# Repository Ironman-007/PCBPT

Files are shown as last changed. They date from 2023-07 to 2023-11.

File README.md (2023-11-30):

# PCBPT (PCB Probe tester)
## The PCBPT_V3 is the latest working version (the one I showed at UIST'23).

This is a system that can help directly connect the schematic of the PCB design with test equipment (oscilloscope. etc,). When doing PCB debugging, we would need to use our hands to hold the oscilloscope probes, and our hands can not be that precise and table. Sometimes our hands are not enough, and we need to go from schematic and PCB layout back and forth to find a proper pad for the signal and place a probe on it.

The PCBPT connects the Sch with the oscilloscope. The user can choose a signal they want to check on the Sch, and the system will choose a proper pad and place a probe on the pad. Then the user can just check the output from the oscilloscope. All the user needs to do is select signals from Sch and check the output.

## PCBPT_V1.0

The first version of PCBPT is here:
https://www.media.mit.edu/projects/pcb-probe-tester/overview/

It's very rough. The machine design is not that perfect. The motor I used is [28BYJ-48](https://www.amazon.com/ELEGOO-28BYJ-48-ULN2003-Stepper-Arduino/dp/B01CP18J4A). It's very slow. The software is not that good, either. I have a separate GUI for the signal choosing. However, what I want is to choose the signal from the EDA, or make a GUI with the Sch and choose the signal from the SCH.

## PCBPT_V2.0
### Mechanical
The new machine design (I really love the Prusa color!).

<p align="center">
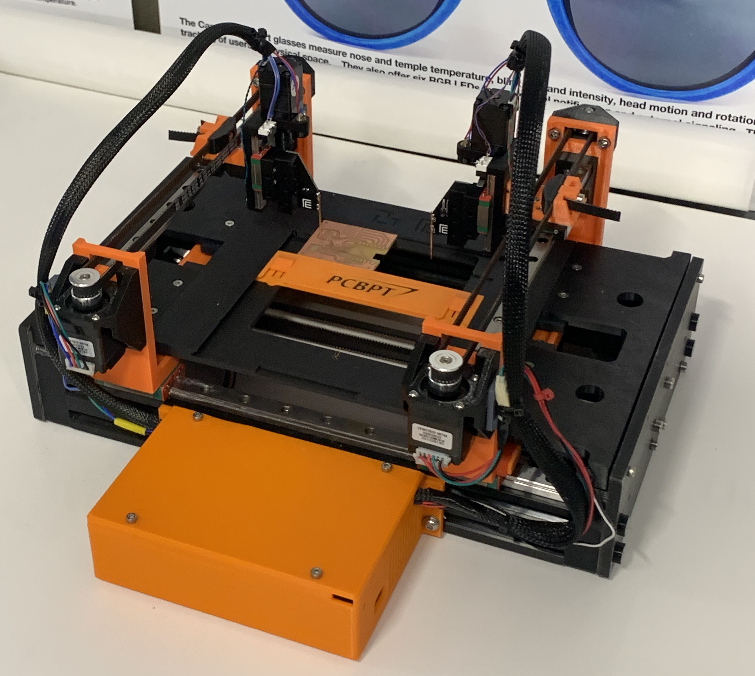
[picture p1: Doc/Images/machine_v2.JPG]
  
</p>

### Electronics
The first version of the main control board is a modular design. Each module can control a stepper motor and a servo. Each module is an RP2040 XIAO + A4988 stepper driver. The host is an ESP32 module.

<p align="center">
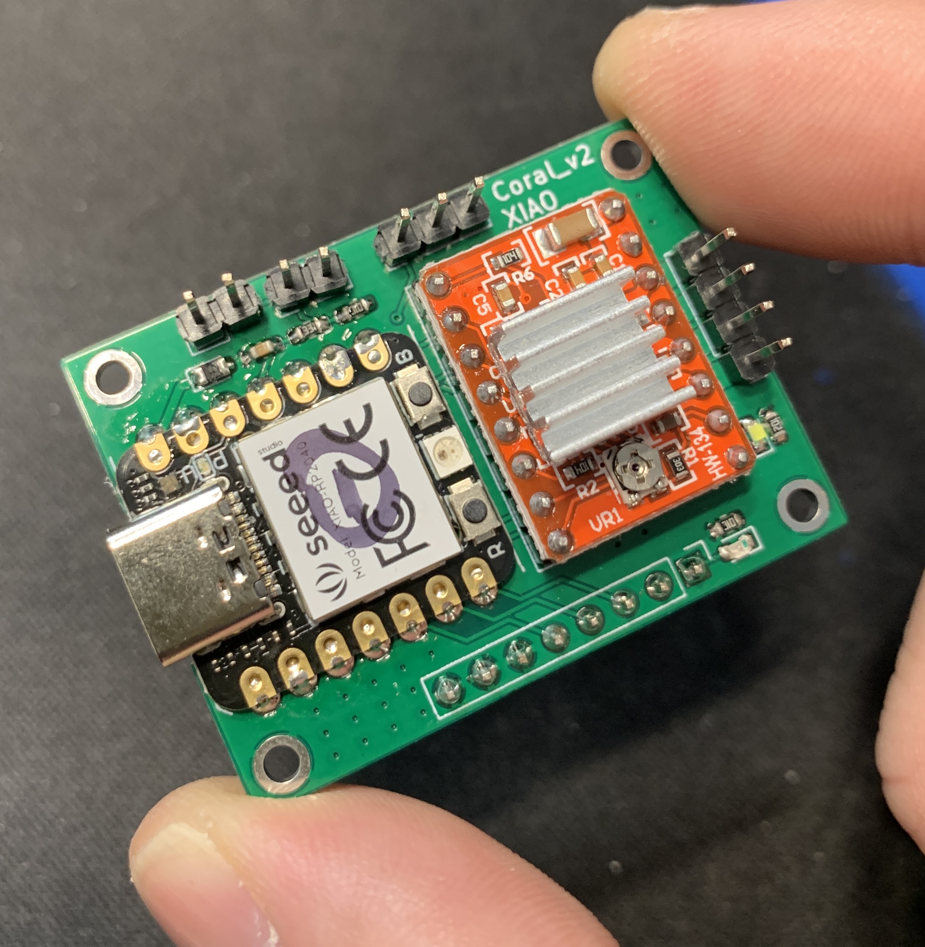
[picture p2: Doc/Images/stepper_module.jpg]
  
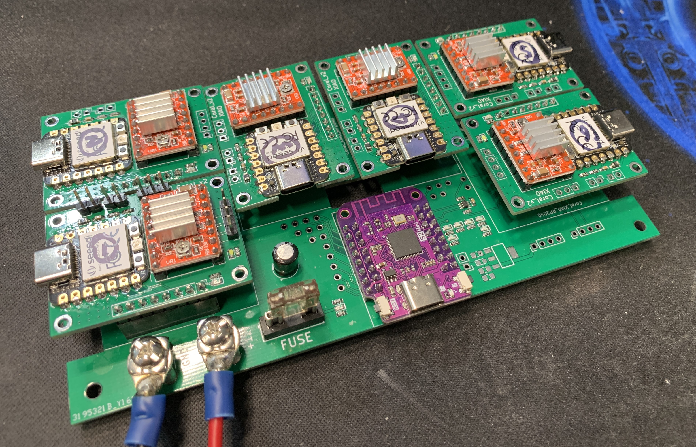
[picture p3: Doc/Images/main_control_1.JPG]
  
</p>

All stepper control modules are connected with the ESP32 module with I2C. The Host runs CircuitPython and is responsible for handling commands from the GUI and sending commands to each stepper control module.
This design is unnecessarily complicated compared with the function of the machine.

The second version of the main control board is a single board. One RPi Pico W module + 6 A4988 driver modules.
The probes are in vertical motion, and each probe is a triangle PCB board with a pogo pin soldered on the edge.

<p align="center">
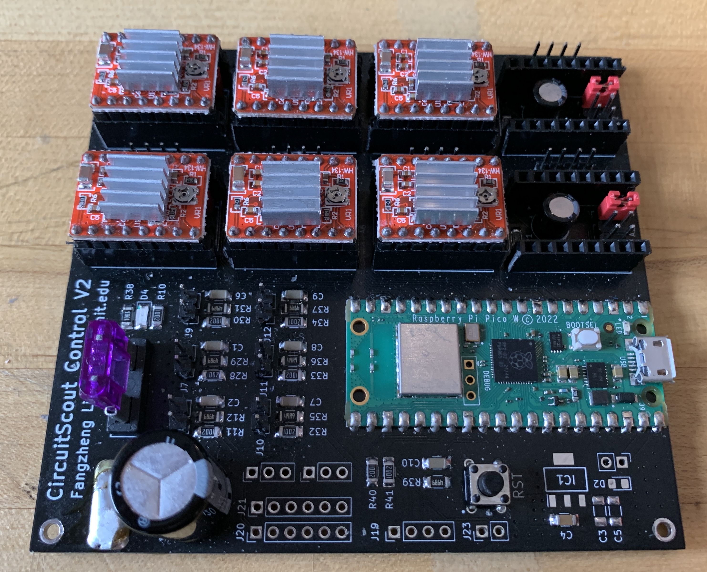
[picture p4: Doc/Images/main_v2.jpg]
  
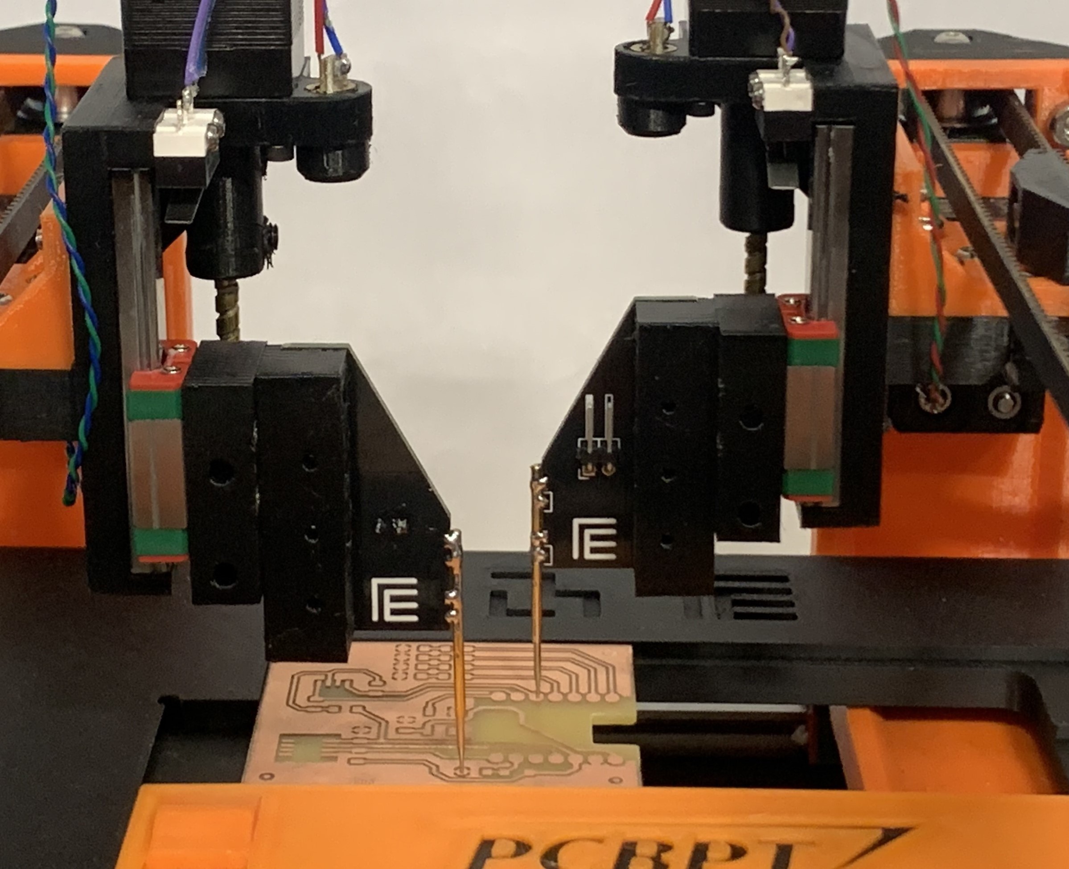
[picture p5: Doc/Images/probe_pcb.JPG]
  
</p>

I use the [PCBWay](https://www.pcbway.com/) service for both the second version of the main control board and the triangle probe PCB board. The quality is good and the production is very fast.

<p align="center">
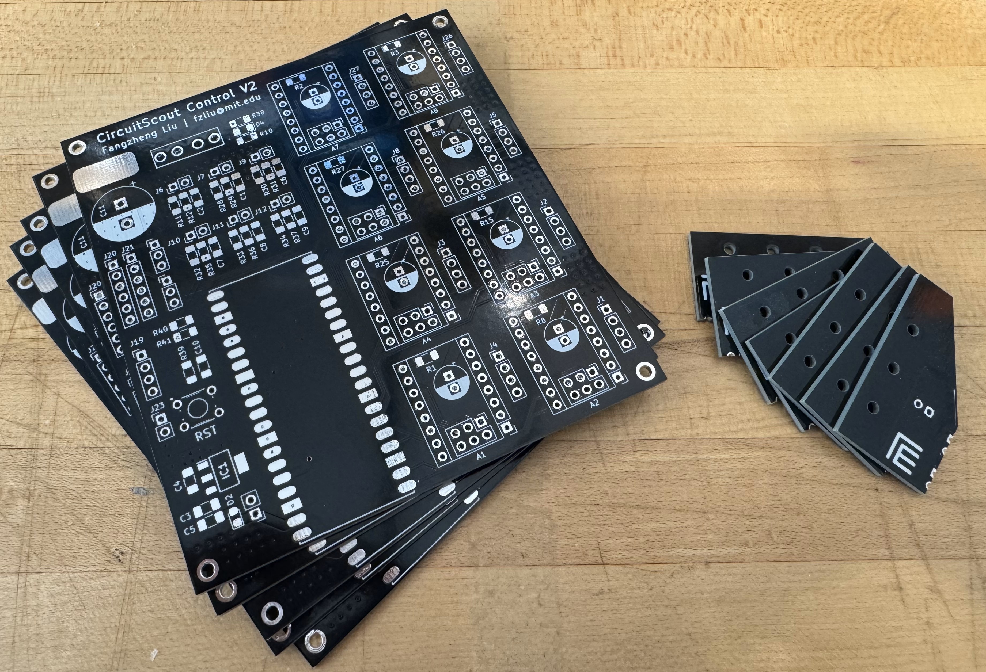
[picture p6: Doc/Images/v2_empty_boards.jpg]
  
</p>

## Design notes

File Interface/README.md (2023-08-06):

# PCBPT Interface

## Introduction

The PCBPT Interface is a web application that allows users to interact with the PCBPT system. It is built using the python [Flask](https://flask.palletsprojects.com/en/2.3.x/) framework and is designed to be run on a standalone raspberry pi. The interface is accessible via a web browser on any device connected to the same network as the raspberry pi (see [Usage](#usage) for more details).

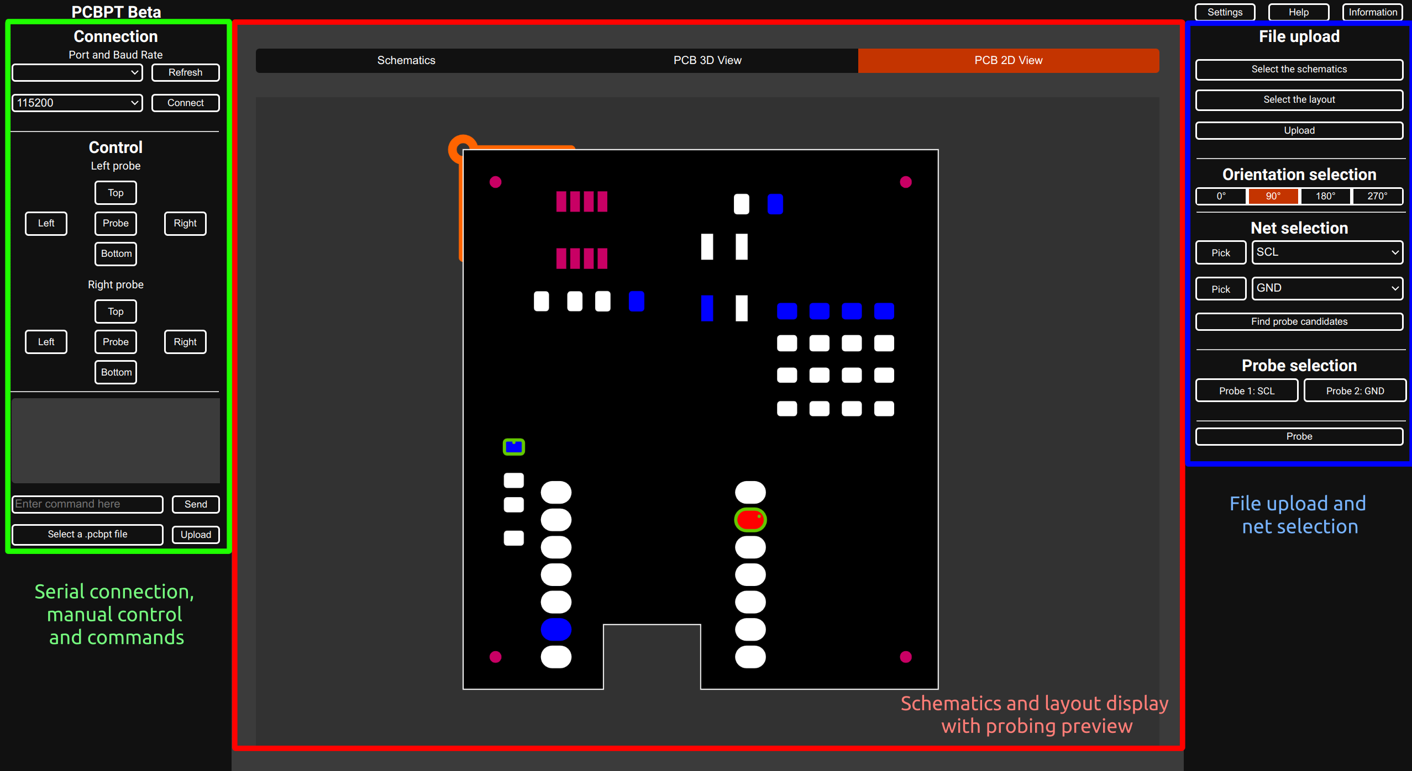
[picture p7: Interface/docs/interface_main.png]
PCBPT Interface


### Features

Using the interface, users can:
- Connect to the probe tester
- Manually control the probe tester
- Send commands and view responses
- Upload a file containing a list of commands set to be executed sequentially
- Upload kKicad schematic and layout files
- Select the nets to be probed
- Manually select the pads to be probed
- Send a probe command to the probe tester

## Installation

Install the required python>=3.9 packages using pip:

```bash
pip install -r requirements.txt
```

## Usage

To run the interface, execute the following command:

```bash
python3 -m gunicorn --worker-class eventlet -w 1 interface:app --reload --bind :8001
```

You can modify the port number by changing the number after the colon in the `--bind` argument. The interface will be accessible at `http://<ip address>:<port number>`, where `<ip address>` is the IP address of the host machine running the interface (127.0.0.1 if on the same machine) and `<port number>` is the port number specified in the `--bind` argument.

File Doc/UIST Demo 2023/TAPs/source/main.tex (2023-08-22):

\documentclass[sigconf]{acmart}

%%
%% \BibTeX command to typeset BibTeX logo in the docs
\AtBeginDocument{%
  \providecommand\BibTeX{{%
    Bib\TeX}}}

%% Rights management information.  This information is sent to you
%% when you complete the rights form.  These commands have SAMPLE
%% values in them; it is your responsibility as an author to replace
%% the commands and values with those provided to you when you
%% complete the rights form.
\copyrightyear{2023} 
\acmYear{2023} 
\setcopyright{rightsretained} 
\acmConference[UIST '23 Adjunct]{The 36th Annual ACM Symposium on User Interface Software and Technology}{October 29-November 1, 2023}{San Francisco, CA, USA}
\acmBooktitle{The 36th Annual ACM Symposium on User Interface Software and Technology (UIST '23 Adjunct), October 29-November 1, 2023, San Francisco, CA, USA}
\acmDOI{10.1145/3586182.3615800}
\acmISBN{979-8-4007-0096-5/23/10}

%%
%%  Uncomment \acmBooktitle if the title of the proceedings is different
%%  from ``Proceedings of ...''!
%%
%%\acmBooktitle{Woodstock '18: ACM Symposium on Neural Gaze Detection,
%%  June 03--05, 2018, Woodstock, NY}
% \acmPrice{15.00}
% \acmISBN{978-1-4503-6708-0/20/04}

%%
%% end of the preamble, start of the body of the document source.
\begin{document}

%%
%% The "title" command has an optional parameter,
%% allowing the author to define a "short title" to be used in page headers.
\title[Printed Circuit Board (PCB) Probe Tester (PCBPT) - a Compact Desktop System that Helps with \\ Automatic PCB Debugging]
{Printed Circuit Board (PCB) Probe Tester (PCBPT) - a Compact Desktop System that Helps with Automatic PCB Debugging}
% \title{Printed Circuit Board (PCB) Probe Tester (PCBPT)
% - a Compact Desktop System that Helps with Automatic PCB Debugging}

%%
%% The "author" command and its associated commands are used to define
%% the authors and their affiliations.
%% Of note is the shared affiliation of the first two authors, and the
%% "authornote" and "authornotemark" commands
%% used to denote shared contribution to the research.
\author{Fangzheng Liu}
\affiliation{%
  \institution{Responsive Environments, MIT Media Lab}
  \city{Cambridge}
  \country{USA}}
\email{fzliu@mit.edu}

\author{Joseph Paradiso}
\affiliation{%
  \institution{Responsive Environments, MIT Media Lab}
  \city{Cambridge}
  \country{USA}}
\email{joep@media.mit.edu}

\begin{abstract}
PCB debugging can be tricky. For example, if we want to use an oscilloscope to measure signals of interest in the PCB, we need to locate them in the schematic and select the appropriate pad for each signal on the PCB layout on which to put the oscilloscope probes. This process hence requires frequent switching between the schematics and the PCB layouts. Moreover, our hands may not be precise and stable enough to accurately place the probes on the pads without causing short circuits with adjacent pins, which can lead to further issues. Additionally, if multiple signals need to be tested, two hands will not be enough. Probe hook clips can be used, but this often necessitates the use of extension wires that must be soldered onto the targeted pads. To streamline the debugging process, we introduce the PCBPT (PCB Probing Tester). This innovative solution seamlessly bridges from schematic to test equipment by using a robotic probe and actuated board holder. By selecting signals of interest directly from a GUI, users can instantly monitor the output on an oscilloscope, significantly improving the effectiveness of the debugging process.
\end{abstract}

%%
%% The code below is generated by the tool at http://dl.acm.org/ccs.cfm.
%% Please copy and paste the code instead of the example below.
%%
\begin{CCSXML}
<ccs2012>
   <concept>
       <concept_id>10003120.10003121.10003129</concept_id>
       <concept_desc>Human-centered computing~Interactive systems and tools</concept_desc>
       <concept_significance>500</concept_significance>
       </concept>
 </ccs2012>
\end{CCSXML}

\ccsdesc[500]{Human-centered computing~Interactive systems and tools}
%%
%% Keywords. The author(s) should pick words that accurately describe
%% the work being presented. Separate the keywords with commas.
\keywords{compact desktop system, PCB, automatic debugging, in-circuit debugging}

% %% A "teaser" image appears between the author and affiliation
% %% information and the body of the document, and typically spans the
% %% page.
% \begin{teaserfigure}
%   \includegraphics[width=\textwidth]{sampleteaser}
%   \caption{Seattle Mariners at Spring Training, 2010.}
%   \Description{Enjoying the baseball game from the third-base
%   seats. Ichiro Suzuki preparing to bat.}
%   \label{fig:teaser}
% \end{teaserfigure}

%%
%% This command processes the author and affiliation and title
%% information and builds the first part of the formatted document.
\maketitle

\section{Introduction}
To enhance the efficiency of debugging processes for hardware engineers and hobbyists, we have developed the PCBPT (PCB Probing Tester). Traditionally, for debugging the function of PCB, we need to measure signals of interest by using test equipment, such as an oscilloscope. This requires frequent switching between schematics and PCB layouts to identify signals of interest and select appropriate pads for probe placement. The manual probing method is prone to errors, such as short-circuiting adjacent pins and causing further issues \cite{automatic_compactpcbdebugging}. Additionally, when multiple signals need to be tested, the limitations of human hands become apparent. Although probe hook clips with extension wires are an alternative, they necessitate soldering on targeting pads, and when the size of the PCB is compact due to application limit, there is no space for extra test points pads for debugging.

A bed-of-nails jig is an alternative. However, it requires the consuming design and production of a jig for each specific PCB design, rendering it inefficient for even minor component position changes since it requires a redesign and production of the jig. Commercial flying probe testers are expensive and bulky, making them unsuitable for hobbyists and small companies.

The PCBPT is a compact desktop tool, and by leveraging the information contained in the PCB layout, and eliminating the need for manual probing, the PCBPT revolutionizes the way debugging is conducted and allows users to select signals of interest and immediately view the output on an oscilloscope. This streamlined workflow significantly enhances the effectiveness of debugging. With the PCBPT, engineers can efficiently interact with their designs during the debugging process.

% It empowers hardware engineers and hobbyists to achieve precise and fast diagnostics without the limitations of traditional methods or the cost and size constraints associated with commercial solutions.

\section{System structure}
The PCBPT works with PCB designed by EAGLE — an electronic design automation (EDA) software for PCB design. The entire system comprises two components: the Data Processing Program and the PCBPT Probe Machine, as illustrated in Fig.\ref{PCBPT_structure}.

\begin{figure}[h]
  \centering
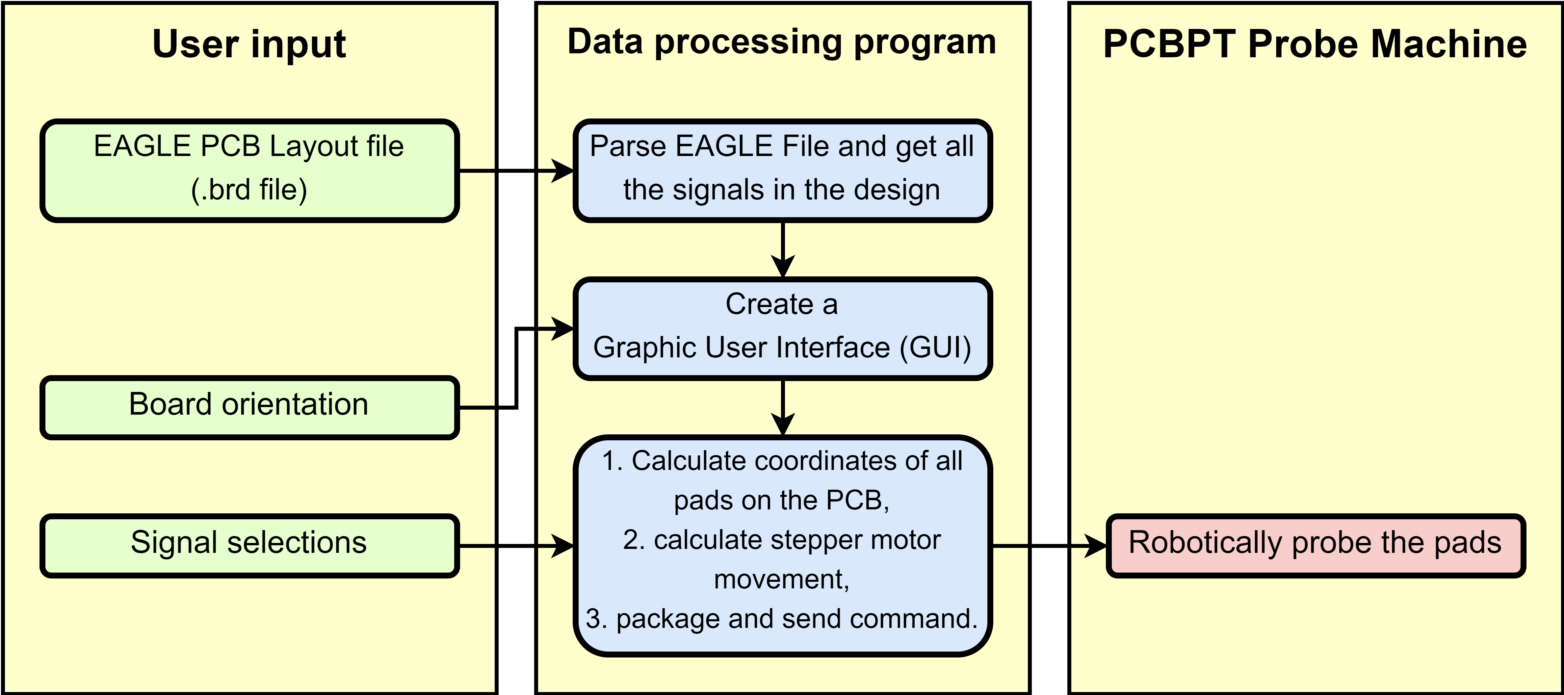
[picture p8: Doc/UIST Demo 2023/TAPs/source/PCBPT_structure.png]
  
  \caption{The PCBPT system structure}
  \label{PCBPT_structure}
  \Description{Structure of the PCBPT system. The system accepts Users input, including EAGLE design files, board orientation and signals to be measured. A program parses the data input and calculates the coordinates of all pads on the PCB. Upon signals selections, the program controls the machine to probe the corresponding pads.}
\end{figure}

\subsection{Data Processing Program}
The Data Processing Program is written in Python and performs several key functions, such as accepting and parsing user input, including the EAGLE PCB layout file (.brd), and the orientation of the tested board on the PCBPT Probe machine. Additionally, it creates a user-friendly GUI for signal selection, calculates PCB pad coordinates, and controls probe movements on the machine.
The EAGLE PCB layout design file is encoded in XML format, making it readily parseable in Python. Upon importing the $.brd$ file, the program extracts and stores comprehensive information about all components and signals within the PCB design. It then generates a user-friendly GUI that displays a list of all signals for selection. Through the GUI, the user can choose specific signals of interest. Subsequently, the program automatically determines the appropriate pads, based on the size of the pads and type of the components for the selected signals and calculates their corresponding coordinates. A command is then issued to the machine to initiate the probing process on the identified pads. The subsequent section will provide a detailed explanation of the coordinate calculation method.

The program generates a GUI (as shown in Fig.\ref{GUI}) to facilitate the user's interaction. As an example, we select the Adafruit LIS3DH breakout board \cite{Adafruit_LIS3DH} to demonstrate its functionality within the GUI.

\begin{figure}[h]
  \centering
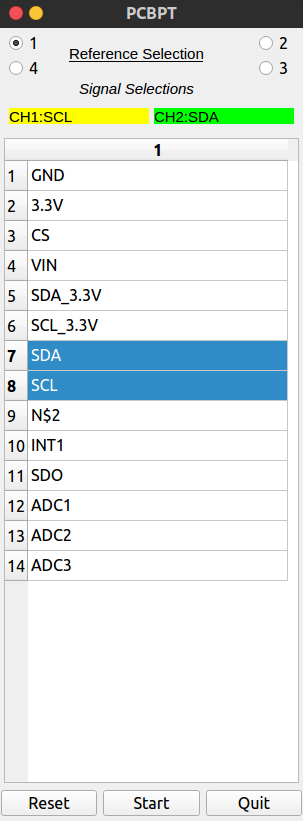
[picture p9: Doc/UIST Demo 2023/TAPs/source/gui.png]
  
  \caption{The GUI for the user to select signals to be measured.}
  \label{GUI}
  \Description{The GUI of the PCBPT. It shows the list of signals in the PCB design, and users can select the desired signals to be measured.}
\end{figure}

\subsection{PCBPT Probe Machine}
The PCBPT Probe Machine is a compact ($35.0cm \times 12.5cm \times 24.8cm$) 3D-printed CNC machine with two probes, as shown in Fig.\ref{machine}. The PCB to be tested is positioned and secured on the machine platform.

\begin{figure}[h]
  \centering
  
  \caption{PCBPT Probe Machine}
  \label{machine}
  \Description{The PCBPT machine --- a CNC machine with two gantries, and each gantry has a probe.}
\end{figure}

The machine utilizes stepper motors for actuation in the XY axis, while tiny linear servos drive the two probes in the Z axis. The electronic system structure of the machine is illustrated in Figure \ref{electronics_structure}. To facilitate the robotic probing of targeted pads, an Arduino Mega2560 board is employed. It receives commands from the Data Processing Program and controls the four steppers for XY-axis movement, as well as the servos for Z-axis movement to probe the targeted pads.

\begin{figure}[h]
  \centering
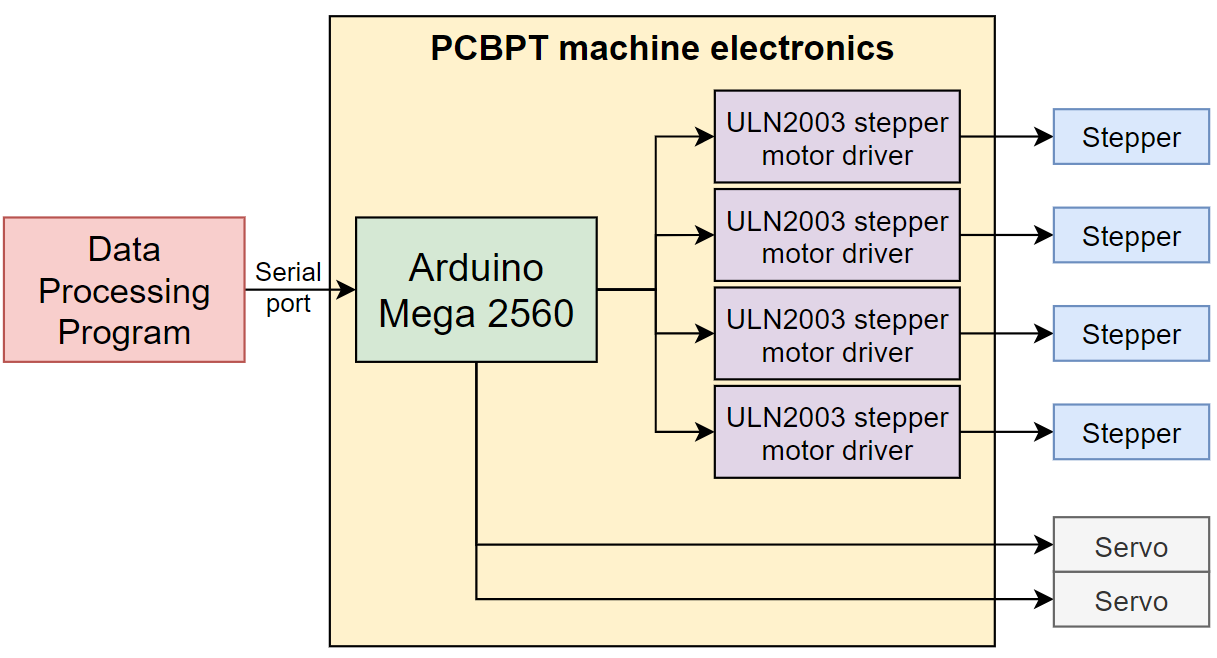
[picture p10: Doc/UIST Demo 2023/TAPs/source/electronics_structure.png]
  
  \caption{PCBPT Probe Machine electronics system}
  \label{electronics_structure}
  \Description{The PCBPT electronics system. The core part is an Arduino Mega 2560 board which is connected to four stepper motor driver modules.}
\end{figure}

Prior to utilization, the machine undergoes calibration to establish the correlation between the stepper motor's steps and the actual distance covered during movement.

\section{Workflow}
This section outlines the workflow for utilizing the PCBPT in automating the process of PCB debugging.

\subsection{Calibration}
To align the coordinates of all pads in the PCB design with the machine's coordinate system, the user must first specify the board's orientation on the holder relative to the PCB layout design through the GUI. Currently, the machine only supports square-shaped PCBs, allowing orientations of $0^{\circ}$, $90^{\circ}$, $180^{\circ}$, and $270^{\circ}$. After selecting an orientation, the user manually controls the machine to probe a chosen pad and records the corresponding movements. By incorporating the orientation and the steps bias, the program utilizes a rotation equation \cite{rotation_equation} to calculate the coordinates of all pads in the machine's coordinate system.

The current calibration approach is straightforward and will benefit from enhancements (e.g., using a camera and image processing for the automatic board, components, and pad detections\cite{inspect_ar}) to improve its effectiveness and accuracy.

\subsection{Probe}
Upon powering on, the machine will automatically position the two probes to their start positions. Once the user selects the desired signals for measurement from the GUI and clicks the "Start" button, the program will send a digital command to the machine that will specify the direction and the number of steps each motor should move. Subsequently, the machine will control the probes to accurately and automatically contact the corresponding pads on the PCB. To facilitate real-time signal analysis, each probe can be connected to a separate channel of an oscilloscope, which instantly visualizes the waveform of the selected signals, as shown in Fig.\ref{result}. In this measurement, we use the Adafruit LIS3DH breakout board as an example and measured the $I^2C$ signals.

\begin{figure}[h]
  \centering
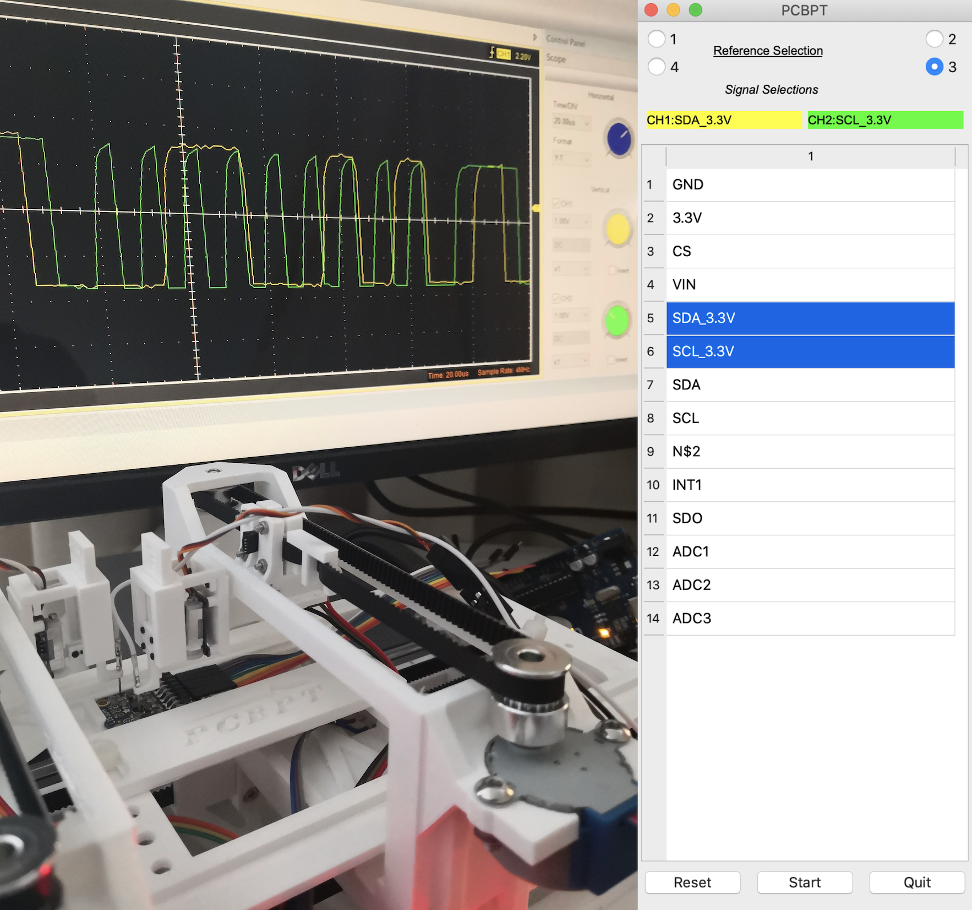
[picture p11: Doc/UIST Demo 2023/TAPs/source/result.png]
  
  \caption{PCBPT automatically probes the desired pads and an oscilloscope visualizes the signals.}
  \label{result}
  \Description{The PCBPT helps with automatic probing the I2C signal on a small PCB.}
\end{figure}

\section{Conclusion}
The PCBPT system introduces an innovative approach by directly connecting the PCB schematic with the signals output, bridging the gap between design and real-world measurements. However, there are identifiable limitations within the current design, For instance, the system currently supports testing only one side of the PCB, employs only two probes, and utilizes a calibration approach that lacks efficiency. Additionally, the dimensions of the PCBs that can be tested are currently restricted to $50mm \times 70mm \times 4mm$. We hope that through further enhancements, this system could be a useful tool for future engineers and hardware hobbyists.  Improvements could include a camera on the probe and allowing the probe to tilt for use in cases where a pad can’t easily be accessed only by vertical movement and/or component shape inhibits easy access to a pad.  It would also be possible to combine simulation or cached data with the signals, displaying for example expected voltage levels and waveforms with the actual data, as used in \cite{boardlab}.

%%
%% The next two lines define the bibliography style to be used, and
%% the bibliography file.
\bibliographystyle{ACM-Reference-Format}
\bibliography{sample-base}

%%
%% If your work has an appendix, this is the place to put it.
\appendix

\end{document}
\endinput
%%
%% End of file `sample-lualatex.tex'.

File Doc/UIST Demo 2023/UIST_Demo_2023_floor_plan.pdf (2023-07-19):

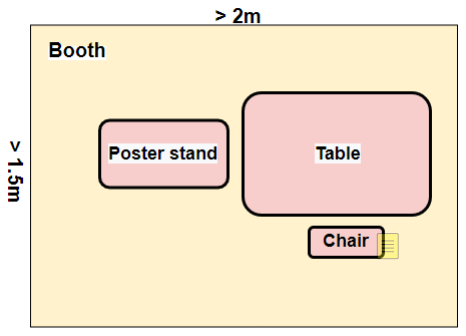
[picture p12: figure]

1

## PCBPT UIST 2023 Demo Floor plan

Fangzheng Liu

- size of the booth: > 2m x 1.5m
- demo hardware components: PCBPT machine (put on table), a monitor (preferred 27in, 24in works, too), a laptop (brought by myself)
- numbers of tables: 1
- chairs: 1
- light or dark environment required: light environment
- power requirements: an power extension cord with at least 2 outlets
- VR setup: None
- poster stand (recommended): yes
- any other equipment or relevant detail: none

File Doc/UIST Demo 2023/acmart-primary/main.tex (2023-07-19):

%%
%% This is file `sample-authordraft.tex',
%% generated with the docstrip utility.
%%
%% The original source files were:
%%
%% samples.dtx  (with options: `authordraft')
%% 
%% IMPORTANT NOTICE:
%% 
%% For the copyright see the source file.
%% 
%% Any modified versions of this file must be renamed
%% with new filenames distinct from sample-authordraft.tex.
%% 
%% For distribution of the original source see the terms
%% for copying and modification in the file samples.dtx.
%% 
%% This generated file may be distributed as long as the
%% original source files, as listed above, are part of the
%% same distribution. (The sources need not necessarily be
%% in the same archive or directory.)
%%
%%
%% Commands for TeXCount
%TC:macro \cite [option:text,text]
%TC:macro \citep [option:text,text]
%TC:macro \citet [option:text,text]
%TC:envir table 0 1
%TC:envir table* 0 1
%TC:envir tabular [ignore] word
%TC:envir displaymath 0 word
%TC:envir math 0 word
%TC:envir comment 0 0
%%
%%
%% The first command in your LaTeX source must be the \documentclass
%% command.
%%
%% For submission and review of your manuscript please change the
%% command to \documentclass[manuscript, screen, review]{acmart}.
%%
%% When submitting camera ready or to TAPS, please change the command
%% to \documentclass[sigconf]{acmart} or whichever template is required
%% for your publication.
%%
%%
\documentclass[sigconf,authordraft]{acmart}

%%
%% \BibTeX command to typeset BibTeX logo in the docs
\AtBeginDocument{%
  \providecommand\BibTeX{{%
    Bib\TeX}}}

%% Rights management information.  This information is sent to you
%% when you complete the rights form.  These commands have SAMPLE
%% values in them; it is your responsibility as an author to replace
%% the commands and values with those provided to you when you
%% complete the rights form.
\setcopyright{acmcopyright}
\copyrightyear{2018}
\acmYear{2018}
\acmDOI{XXXXXXX.XXXXXXX}

%% These commands are for a PROCEEDINGS abstract or paper.
\acmConference[Conference acronym 'XX]{Make sure to enter the correct
  conference title from your rights confirmation emai}{June 03--05,
  2018}{Woodstock, NY}
%%
%%  Uncomment \acmBooktitle if the title of the proceedings is different
%%  from ``Proceedings of ...''!
%%
%%\acmBooktitle{Woodstock '18: ACM Symposium on Neural Gaze Detection,
%%  June 03--05, 2018, Woodstock, NY}
\acmPrice{15.00}
\acmISBN{978-1-4503-XXXX-X/18/06}

%%
%% Submission ID.
%% Use this when submitting an article to a sponsored event. You'll
%% receive a unique submission ID from the organizers
%% of the event, and this ID should be used as the parameter to this command.
%%\acmSubmissionID{123-A56-BU3}

%%
%% For managing citations, it is recommended to use bibliography
%% files in BibTeX format.
%%
%% You can then either use BibTeX with the ACM-Reference-Format style,
%% or BibLaTeX with the acmnumeric or acmauthoryear sytles, that include
%% support for advanced citation of software artefact from the
%% biblatex-software package, also separately available on CTAN.
%%
%% Look at the sample-*-biblatex.tex files for templates showcasing
%% the biblatex styles.
%%

%%
%% The majority of ACM publications use numbered citations and
%% references.  The command \citestyle{authoryear} switches to the
%% "author year" style.
%%
%% If you are preparing content for an event
%% sponsored by ACM SIGGRAPH, you must use the "author year" style of
%% citations and references.
%% Uncommenting
%% the next command will enable that style.
%%\citestyle{acmauthoryear}

%%
%% end of the preamble, start of the body of the document source.
\begin{document}

%%
%% The "title" command has an optional parameter,
%% allowing the author to define a "short title" to be used in page headers.
\title{The Name of the Title Is Hope}

%%
%% The "author" command and its associated commands are used to define
%% the authors and their affiliations.
%% Of note is the shared affiliation of the first two authors, and the
%% "authornote" and "authornotemark" commands
%% used to denote shared contribution to the research.
\author{Ben Trovato}
\authornote{Both authors contributed equally to this research.}
\email{trovato@corporation.com}
\orcid{1234-5678-9012}
\author{G.K.M. Tobin}
\authornotemark[1]
\email{webmaster@marysville-ohio.com}
\affiliation{%
  \institution{Institute for Clarity in Documentation}
  \streetaddress{P.O. Box 1212}
  \city{Dublin}
  \state{Ohio}
  \country{USA}
  \postcode{43017-6221}
}

\author{Lars Th{\o}rv{\"a}ld}
\affiliation{%
  \institution{The Th{\o}rv{\"a}ld Group}
  \streetaddress{1 Th{\o}rv{\"a}ld Circle}
  \city{Hekla}
  \country{Iceland}}
\email{larst@affiliation.org}

\author{Valerie B\'eranger}
\affiliation{%
  \institution{Inria Paris-Rocquencourt}
  \city{Rocquencourt}
  \country{France}
}

\author{Aparna Patel}
\affiliation{%
 \institution{Rajiv Gandhi University}
 \streetaddress{Rono-Hills}
 \city{Doimukh}
 \state{Arunachal Pradesh}
 \country{India}}

\author{Huifen Chan}
\affiliation{%
  \institution{Tsinghua University}
  \streetaddress{30 Shuangqing Rd}
  \city{Haidian Qu}
  \state{Beijing Shi}
  \country{China}}

\author{Charles Palmer}
\affiliation{%
  \institution{Palmer Research Laboratories}
  \streetaddress{8600 Datapoint Drive}
  \city{San Antonio}
  \state{Texas}
  \country{USA}
  \postcode{78229}}
\email{cpalmer@prl.com}

\author{John Smith}
\affiliation{%
  \institution{The Th{\o}rv{\"a}ld Group}
  \streetaddress{1 Th{\o}rv{\"a}ld Circle}
  \city{Hekla}
  \country{Iceland}}
\email{jsmith@affiliation.org}

\author{Julius P. Kumquat}
\affiliation{%
  \institution{The Kumquat Consortium}
  \city{New York}
  \country{USA}}
\email{jpkumquat@consortium.net}

%%
%% By default, the full list of authors will be used in the page
%% headers. Often, this list is too long, and will overlap
%% other information printed in the page headers. This command allows
%% the author to define a more concise list
%% of authors' names for this purpose.
\renewcommand{\shortauthors}{Trovato et al.}

%%
%% The abstract is a short summary of the work to be presented in the
%% article.
\begin{abstract}
  A clear and well-documented \LaTeX\ document is presented as an
  article formatted for publication by ACM in a conference proceedings
  or journal publication. Based on the ``acmart'' document class, this
  article presents and explains many of the common variations, as well
  as many of the formatting elements an author may use in the
  preparation of the documentation of their work.
\end{abstract}

%%
%% The code below is generated by the tool at http://dl.acm.org/ccs.cfm.
%% Please copy and paste the code instead of the example below.
%%
\begin{CCSXML}
<ccs2012>
 <concept>
  <concept_id>10010520.10010553.10010562</concept_id>
  <concept_desc>Computer systems organization~Embedded systems</concept_desc>
  <concept_significance>500</concept_significance>
 </concept>
 <concept>
  <concept_id>10010520.10010575.10010755</concept_id>
  <concept_desc>Computer systems organization~Redundancy</concept_desc>
  <concept_significance>300</concept_significance>
 </concept>
 <concept>
  <concept_id>10010520.10010553.10010554</concept_id>
  <concept_desc>Computer systems organization~Robotics</concept_desc>
  <concept_significance>100</concept_significance>
 </concept>
 <concept>
  <concept_id>10003033.10003083.10003095</concept_id>
  <concept_desc>Networks~Network reliability</concept_desc>
  <concept_significance>100</concept_significance>
 </concept>
</ccs2012>
\end{CCSXML}

\ccsdesc[500]{Computer systems organization~Embedded systems}
\ccsdesc[300]{Computer systems organization~Redundancy}
\ccsdesc{Computer systems organization~Robotics}
\ccsdesc[100]{Networks~Network reliability}

%%
%% Keywords. The author(s) should pick words that accurately describe
%% the work being presented. Separate the keywords with commas.
\keywords{datasets, neural networks, gaze detection, text tagging}
%% A "teaser" image appears between the author and affiliation
%% information and the body of the document, and typically spans the
%% page.
\begin{teaserfigure}
  
  \caption{Seattle Mariners at Spring Training, 2010.}
  \Description{Enjoying the baseball game from the third-base
  seats. Ichiro Suzuki preparing to bat.}
  \label{fig:teaser}
\end{teaserfigure}

\received{20 February 2007}
\received[revised]{12 March 2009}
\received[accepted]{5 June 2009}

%%
%% This command processes the author and affiliation and title
%% information and builds the first part of the formatted document.
\maketitle

\section{Introduction}
ACM's consolidated article template, introduced in 2017, provides a
consistent \LaTeX\ style for use across ACM publications, and
incorporates accessibility and metadata-extraction functionality
necessary for future Digital Library endeavors. Numerous ACM and
SIG-specific \LaTeX\ templates have been examined, and their unique
features incorporated into this single new template.

If you are new to publishing with ACM, this document is a valuable
guide to the process of preparing your work for publication. If you
have published with ACM before, this document provides insight and
instruction into more recent changes to the article template.

The ``\verb|acmart|'' document class can be used to prepare articles
for any ACM publication --- conference or journal, and for any stage
of publication, from review to final ``camera-ready'' copy, to the
author's own version, with {\itshape very} few changes to the source.

\section{Template Overview}
As noted in the introduction, the ``\verb|acmart|'' document class can
be used to prepare many different kinds of documentation --- a
double-blind initial submission of a full-length technical paper, a
two-page SIGGRAPH Emerging Technologies abstract, a ``camera-ready''
journal article, a SIGCHI Extended Abstract, and more --- all by
selecting the appropriate {\itshape template style} and {\itshape
  template parameters}.

This document will explain the major features of the document
class. For further information, the {\itshape \LaTeX\ User's Guide} is
available from
\url{https://www.acm.org/publications/proceedings-template}.

\subsection{Template Styles}

The primary parameter given to the ``\verb|acmart|'' document class is
the {\itshape template style} which corresponds to the kind of publication
or SIG publishing the work. This parameter is enclosed in square
brackets and is a part of the {\verb|documentclass|} command:
\begin{verbatim}
  \documentclass[STYLE]{acmart}
\end{verbatim}

Journals use one of three template styles. All but three ACM journals
use the {\verb|acmsmall|} template style:
\begin{itemize}
\item {\texttt{acmsmall}}: The default journal template style.
\item {\texttt{acmlarge}}: Used by JOCCH and TAP.
\item {\texttt{acmtog}}: Used by TOG.
\end{itemize}

The majority of conference proceedings documentation will use the {\verb|acmconf|} template style.
\begin{itemize}
\item {\texttt{acmconf}}: The default proceedings template style.
\item{\texttt{sigchi}}: Used for SIGCHI conference articles.
\item{\texttt{sigplan}}: Used for SIGPLAN conference articles.
\end{itemize}

\subsection{Template Parameters}

In addition to specifying the {\itshape template style} to be used in
formatting your work, there are a number of {\itshape template parameters}
which modify some part of the applied template style. A complete list
of these parameters can be found in the {\itshape \LaTeX\ User's Guide.}

Frequently-used parameters, or combinations of parameters, include:
\begin{itemize}
\item {\texttt{anonymous,review}}: Suitable for a ``double-blind''
  conference submission. Anonymizes the work and includes line
  numbers. Use with the \texttt{\acmSubmissionID} command to print the
  submission's unique ID on each page of the work.
\item{\texttt{authorversion}}: Produces a version of the work suitable
  for posting by the author.
\item{\texttt{screen}}: Produces colored hyperlinks.
\end{itemize}

This document uses the following string as the first command in the
source file:
\begin{verbatim}
\documentclass[sigconf,authordraft]{acmart}
\end{verbatim}

\section{Modifications}

Modifying the template --- including but not limited to: adjusting
margins, typeface sizes, line spacing, paragraph and list definitions,
and the use of the \verb|\vspace| command to manually adjust the
vertical spacing between elements of your work --- is not allowed.

{\bfseries Your document will be returned to you for revision if
  modifications are discovered.}

\section{Typefaces}

The ``\verb|acmart|'' document class requires the use of the
``Libertine'' typeface family. Your \TeX\ installation should include
this set of packages. Please do not substitute other typefaces. The
``\verb|lmodern|'' and ``\verb|ltimes|'' packages should not be used,
as they will override the built-in typeface families.

\section{Title Information}

The title of your work should use capital letters appropriately -
\url{https://capitalizemytitle.com/} has useful rules for
capitalization. Use the {\verb|title|} command to define the title of
your work. If your work has a subtitle, define it with the
{\verb|subtitle|} command.  Do not insert line breaks in your title.

If your title is lengthy, you must define a short version to be used
in the page headers, to prevent overlapping text. The \verb|title|
command has a ``short title'' parameter:
\begin{verbatim}
  \title[short title]{full title}
\end{verbatim}

\section{Authors and Affiliations}

Each author must be defined separately for accurate metadata
identification.  As an exception, multiple authors may share one
affiliation. Authors' names should not be abbreviated; use full first
names wherever possible. Include authors' e-mail addresses whenever
possible.

Grouping authors' names or e-mail addresses, or providing an ``e-mail
alias,'' as shown below, is not acceptable:
\begin{verbatim}
  \author{Brooke Aster, David Mehldau}
  \email{dave,judy,steve@university.edu}
  \email{firstname.lastname@phillips.org}
\end{verbatim}

The \verb|authornote| and \verb|authornotemark| commands allow a note
to apply to multiple authors --- for example, if the first two authors
of an article contributed equally to the work.

If your author list is lengthy, you must define a shortened version of
the list of authors to be used in the page headers, to prevent
overlapping text. The following command should be placed just after
the last \verb|\author{}| definition:
\begin{verbatim}
  \renewcommand{\shortauthors}{McCartney, et al.}
\end{verbatim}
Omitting this command will force the use of a concatenated list of all
of the authors' names, which may result in overlapping text in the
page headers.

The article template's documentation, available at
\url{https://www.acm.org/publications/proceedings-template}, has a
complete explanation of these commands and tips for their effective
use.

Note that authors' addresses are mandatory for journal articles.

\section{Rights Information}

Authors of any work published by ACM will need to complete a rights
form. Depending on the kind of work, and the rights management choice
made by the author, this may be copyright transfer, permission,
license, or an OA (open access) agreement.

Regardless of the rights management choice, the author will receive a
copy of the completed rights form once it has been submitted. This
form contains \LaTeX\ commands that must be copied into the source
document. When the document source is compiled, these commands and
their parameters add formatted text to several areas of the final
document:
\begin{itemize}
\item the ``ACM Reference Format'' text on the first page.
\item the ``rights management'' text on the first page.
\item the conference information in the page header(s).
\end{itemize}

Rights information is unique to the work; if you are preparing several
works for an event, make sure to use the correct set of commands with
each of the works.

The ACM Reference Format text is required for all articles over one
page in length, and is optional for one-page articles (abstracts).

\section{CCS Concepts and User-Defined Keywords}

Two elements of the ``acmart'' document class provide powerful
taxonomic tools for you to help readers find your work in an online
search.

The ACM Computing Classification System ---
\url{https://www.acm.org/publications/class-2012} --- is a set of
classifiers and concepts that describe the computing
discipline. Authors can select entries from this classification
system, via \url{https://dl.acm.org/ccs/ccs.cfm}, and generate the
commands to be included in the \LaTeX\ source.

User-defined keywords are a comma-separated list of words and phrases
of the authors' choosing, providing a more flexible way of describing
the research being presented.

CCS concepts and user-defined keywords are required for for all
articles over two pages in length, and are optional for one- and
two-page articles (or abstracts).

\section{Sectioning Commands}

Your work should use standard \LaTeX\ sectioning commands:
\verb|section|, \verb|subsection|, \verb|subsubsection|, and
\verb|paragraph|. They should be numbered; do not remove the numbering
from the commands.

Simulating a sectioning command by setting the first word or words of
a paragraph in boldface or italicized text is {\bfseries not allowed.}

\section{Tables}

The ``\verb|acmart|'' document class includes the ``\verb|booktabs|''
package --- \url{https://ctan.org/pkg/booktabs} --- for preparing
high-quality tables.

Table captions are placed {\itshape above} the table.

Because tables cannot be split across pages, the best placement for
them is typically the top of the page nearest their initial cite.  To
ensure this proper ``floating'' placement of tables, use the
environment \textbf{table} to enclose the table's contents and the
table caption.  The contents of the table itself must go in the
\textbf{tabular} environment, to be aligned properly in rows and
columns, with the desired horizontal and vertical rules.  Again,
detailed instructions on \textbf{tabular} material are found in the
\textit{\LaTeX\ User's Guide}.

Immediately following this sentence is the point at which
Table~\ref{tab:freq} is included in the input file; compare the
placement of the table here with the table in the printed output of
this document.

\begin{table}
  \caption{Frequency of Special Characters}
  \label{tab:freq}
  \begin{tabular}{ccl}
    \toprule
    Non-English or Math&Frequency&Comments\\
    \midrule
    \O & 1 in 1,000& For Swedish names\\
    $\pi$ & 1 in 5& Common in math\\
    \$ & 4 in 5 & Used in business\\
    $\Psi^2_1$ & 1 in 40,000& Unexplained usage\\
  \bottomrule
\end{tabular}
\end{table}

To set a wider table, which takes up the whole width of the page's
live area, use the environment \textbf{table*} to enclose the table's
contents and the table caption.  As with a single-column table, this
wide table will ``float'' to a location deemed more
desirable. Immediately following this sentence is the point at which
Table~\ref{tab:commands} is included in the input file; again, it is
instructive to compare the placement of the table here with the table
in the printed output of this document.

\begin{table*}
  \caption{Some Typical Commands}
  \label{tab:commands}
  \begin{tabular}{ccl}
    \toprule
    Command &A Number & Comments\\
    \midrule
    \texttt{{\char'134}author} & 100& Author \\
    \texttt{{\char'134}table}& 300 & For tables\\
    \texttt{{\char'134}table*}& 400& For wider tables\\
    \bottomrule
  \end{tabular}
\end{table*}

Always use midrule to separate table header rows from data rows, and
use it only for this purpose. This enables assistive technologies to
recognise table headers and support their users in navigating tables
more easily.

\section{Math Equations}
You may want to display math equations in three distinct styles:
inline, numbered or non-numbered display.  Each of the three are
discussed in the next sections.

\subsection{Inline (In-text) Equations}
A formula that appears in the running text is called an inline or
in-text formula.  It is produced by the \textbf{math} environment,
which can be invoked with the usual
\texttt{{\char'134}begin\,\ldots{\char'134}end} construction or with
the short form \texttt{\$\,\ldots\$}. You can use any of the symbols
and structures, from $\alpha$ to $\omega$, available in
\LaTeX~\cite{Lamport:LaTeX}; this section will simply show a few
examples of in-text equations in context. Notice how this equation:
\begin{math}
  \lim_{n\rightarrow \infty}x=0
\end{math},
set here in in-line math style, looks slightly different when
set in display style.  (See next section).

\subsection{Display Equations}
A numbered display equation---one set off by vertical space from the
text and centered horizontally---is produced by the \textbf{equation}
environment. An unnumbered display equation is produced by the
\textbf{displaymath} environment.

Again, in either environment, you can use any of the symbols and
structures available in \LaTeX\@; this section will just give a couple
of examples of display equations in context.  First, consider the
equation, shown as an inline equation above:
\begin{equation}
  \lim_{n\rightarrow \infty}x=0
\end{equation}
Notice how it is formatted somewhat differently in
the \textbf{displaymath}
environment.  Now, we'll enter an unnumbered equation:
\begin{displaymath}
  \sum_{i=0}^{\infty} x + 1
\end{displaymath}
and follow it with another numbered equation:
\begin{equation}
  \sum_{i=0}^{\infty}x_i=\int_{0}^{\pi+2} f
\end{equation}
just to demonstrate \LaTeX's able handling of numbering.

\section{Figures}

The ``\verb|figure|'' environment should be used for figures. One or
more images can be placed within a figure. If your figure contains
third-party material, you must clearly identify it as such, as shown
in the example below.
\begin{figure}[h]
  \centering
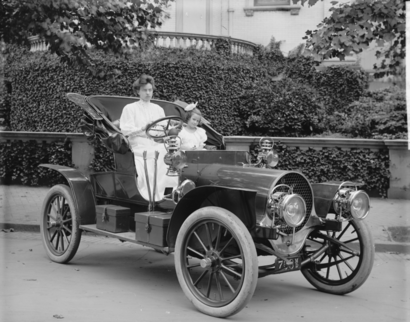
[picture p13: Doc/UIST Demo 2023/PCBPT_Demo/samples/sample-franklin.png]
  
  \caption{1907 Franklin Model D roadster. Photograph by Harris \&
    Ewing, Inc. [Public domain], via Wikimedia
    Commons. (\url{https://goo.gl/VLCRBB}).}
  \Description{A woman and a girl in white dresses sit in an open car.}
\end{figure}

Your figures should contain a caption which describes the figure to
the reader.

Figure captions are placed {\itshape below} the figure.

Every figure should also have a figure description unless it is purely
decorative. These descriptions convey what’s in the image to someone
who cannot see it. They are also used by search engine crawlers for
indexing images, and when images cannot be loaded.

A figure description must be unformatted plain text less than 2000
characters long (including spaces).  {\bfseries Figure descriptions
  should not repeat the figure caption – their purpose is to capture
  important information that is not already provided in the caption or
  the main text of the paper.} For figures that convey important and
complex new information, a short text description may not be
adequate. More complex alternative descriptions can be placed in an
appendix and referenced in a short figure description. For example,
provide a data table capturing the information in a bar chart, or a
structured list representing a graph.  For additional information
regarding how best to write figure descriptions and why doing this is
so important, please see
\url{https://www.acm.org/publications/taps/describing-figures/}.

\subsection{The ``Teaser Figure''}

A ``teaser figure'' is an image, or set of images in one figure, that
are placed after all author and affiliation information, and before
the body of the article, spanning the page. If you wish to have such a
figure in your article, place the command immediately before the
\verb|\maketitle| command:
\begin{verbatim}
  \begin{teaserfigure}
    
    \caption{figure caption}
    \Description{figure description}
  \end{teaserfigure}
\end{verbatim}

\section{Citations and Bibliographies}

The use of \BibTeX\ for the preparation and formatting of one's
references is strongly recommended. Authors' names should be complete
--- use full first names (``Donald E. Knuth'') not initials
(``D. E. Knuth'') --- and the salient identifying features of a
reference should be included: title, year, volume, number, pages,
article DOI, etc.

The bibliography is included in your source document with these two
commands, placed just before the \verb|\end{document}| command:
\begin{verbatim}
  \bibliographystyle{ACM-Reference-Format}
  \bibliography{bibfile}
\end{verbatim}
where ``\verb|bibfile|'' is the name, without the ``\verb|.bib|''
suffix, of the \BibTeX\ file.

Citations and references are numbered by default. A small number of
ACM publications have citations and references formatted in the
``author year'' style; for these exceptions, please include this
command in the {\bfseries preamble} (before the command
``\verb|\begin{document}|'') of your \LaTeX\ source:
\begin{verbatim}
  \citestyle{acmauthoryear}
\end{verbatim}

  Some examples.  A paginated journal article \cite{Abril07}, an
  enumerated journal article \cite{Cohen07}, a reference to an entire
  issue \cite{JCohen96}, a monograph (whole book) \cite{Kosiur01}, a
  monograph/whole book in a series (see 2a in spec. document)
  \cite{Harel79}, a divisible-book such as an anthology or compilation
  \cite{Editor00} followed by the same example, however we only output
  the series if the volume number is given \cite{Editor00a} (so
  Editor00a's series should NOT be present since it has no vol. no.),
  a chapter in a divisible book \cite{Spector90}, a chapter in a
  divisible book in a series \cite{Douglass98}, a multi-volume work as
  book \cite{Knuth97}, a couple of articles in a proceedings (of a
  conference, symposium, workshop for example) (paginated proceedings
  article) \cite{Andler79, Hagerup1993}, a proceedings article with
  all possible elements \cite{Smith10}, an example of an enumerated
  proceedings article \cite{VanGundy07}, an informally published work
  \cite{Harel78}, a couple of preprints \cite{Bornmann2019,
    AnzarootPBM14}, a doctoral dissertation \cite{Clarkson85}, a
  master's thesis: \cite{anisi03}, an online document / world wide web
  resource \cite{Thornburg01, Ablamowicz07, Poker06}, a video game
  (Case 1) \cite{Obama08} and (Case 2) \cite{Novak03} and \cite{Lee05}
  and (Case 3) a patent \cite{JoeScientist001}, work accepted for
  publication \cite{rous08}, 'YYYYb'-test for prolific author
  \cite{SaeediMEJ10} and \cite{SaeediJETC10}. Other cites might
  contain 'duplicate' DOI and URLs (some SIAM articles)
  \cite{Kirschmer:2010:AEI:1958016.1958018}. Boris / Barbara Beeton:
  multi-volume works as books \cite{MR781536} and \cite{MR781537}. A
  couple of citations with DOIs:
  \cite{2004:ITE:1009386.1010128,Kirschmer:2010:AEI:1958016.1958018}. Online
  citations: \cite{TUGInstmem, Thornburg01, CTANacmart}.
  Artifacts: \cite{R} and \cite{UMassCitations}.

\section{Acknowledgments}

Identification of funding sources and other support, and thanks to
individuals and groups that assisted in the research and the
preparation of the work should be included in an acknowledgment
section, which is placed just before the reference section in your
document.

This section has a special environment:
\begin{verbatim}
  \begin{acks}
  ...
  \end{acks}
\end{verbatim}
so that the information contained therein can be more easily collected
during the article metadata extraction phase, and to ensure
consistency in the spelling of the section heading.

Authors should not prepare this section as a numbered or unnumbered {\verb|\section|}; please use the ``{\verb|acks|}'' environment.

\section{Appendices}

If your work needs an appendix, add it before the
``\verb|\end{document}|'' command at the conclusion of your source
document.

Start the appendix with the ``\verb|appendix|'' command:
\begin{verbatim}
  \appendix
\end{verbatim}
and note that in the appendix, sections are lettered, not
numbered. This document has two appendices, demonstrating the section
and subsection identification method.

\section{Multi-language papers}

Papers may be written in languages other than English or include
titles, subtitles, keywords and abstracts in different languages (as a
rule, a paper in a language other than English should include an
English title and an English abstract).  Use \verb|language=...| for
every language used in the paper.  The last language indicated is the
main language of the paper.  For example, a French paper with
additional titles and abstracts in English and German may start with
the following command
\begin{verbatim}
\documentclass[sigconf, language=english, language=german,
               language=french]{acmart}
\end{verbatim}

The title, subtitle, keywords and abstract will be typeset in the main
language of the paper.  The commands \verb|\translatedXXX|, \verb|XXX|
begin title, subtitle and keywords, can be used to set these elements
in the other languages.  The environment \verb|translatedabstract| is
used to set the translation of the abstract.  These commands and
environment have a mandatory first argument: the language of the
second argument.  See \verb|sample-sigconf-i13n.tex| file for examples
of their usage.

\section{SIGCHI Extended Abstracts}

The ``\verb|sigchi-a|'' template style (available only in \LaTeX\ and
not in Word) produces a landscape-orientation formatted article, with
a wide left margin. Three environments are available for use with the
``\verb|sigchi-a|'' template style, and produce formatted output in
the margin:
\begin{description}
\item[\texttt{sidebar}:]  Place formatted text in the margin.
\item[\texttt{marginfigure}:] Place a figure in the margin.
\item[\texttt{margintable}:] Place a table in the margin.
\end{description}

%%
%% The acknowledgments section is defined using the "acks" environment
%% (and NOT an unnumbered section). This ensures the proper
%% identification of the section in the article metadata, and the
%% consistent spelling of the heading.
\begin{acks}
To Robert, for the bagels and explaining CMYK and color spaces.
\end{acks}

%%
%% The next two lines define the bibliography style to be used, and
%% the bibliography file.
\bibliographystyle{ACM-Reference-Format}
\bibliography{sample-base}

%%
%% If your work has an appendix, this is the place to put it.
\appendix

\section{Research Methods}

\subsection{Part One}

Lorem ipsum dolor sit amet, consectetur adipiscing elit. Morbi
malesuada, quam in pulvinar varius, metus nunc fermentum urna, id
sollicitudin purus odio sit amet enim. Aliquam ullamcorper eu ipsum
vel mollis. Curabitur quis dictum nisl. Phasellus vel semper risus, et
lacinia dolor. Integer ultricies commodo sem nec semper.

\subsection{Part Two}

Etiam commodo feugiat nisl pulvinar pellentesque. Etiam auctor sodales
ligula, non varius nibh pulvinar semper. Suspendisse nec lectus non
ipsum convallis congue hendrerit vitae sapien. Donec at laoreet
eros. Vivamus non purus placerat, scelerisque diam eu, cursus
ante. Etiam aliquam tortor auctor efficitur mattis.

\section{Online Resources}

Nam id fermentum dui. Suspendisse sagittis tortor a nulla mollis, in
pulvinar ex pretium. Sed interdum orci quis metus euismod, et sagittis
enim maximus. Vestibulum gravida massa ut felis suscipit
congue. Quisque mattis elit a risus ultrices commodo venenatis eget
dui. Etiam sagittis eleifend elementum.

Nam interdum magna at lectus dignissim, ac dignissim lorem
rhoncus. Maecenas eu arcu ac neque placerat aliquam. Nunc pulvinar
massa et mattis lacinia.

\end{document}
\endinput
%%
%% End of file `sample-authordraft.tex'.

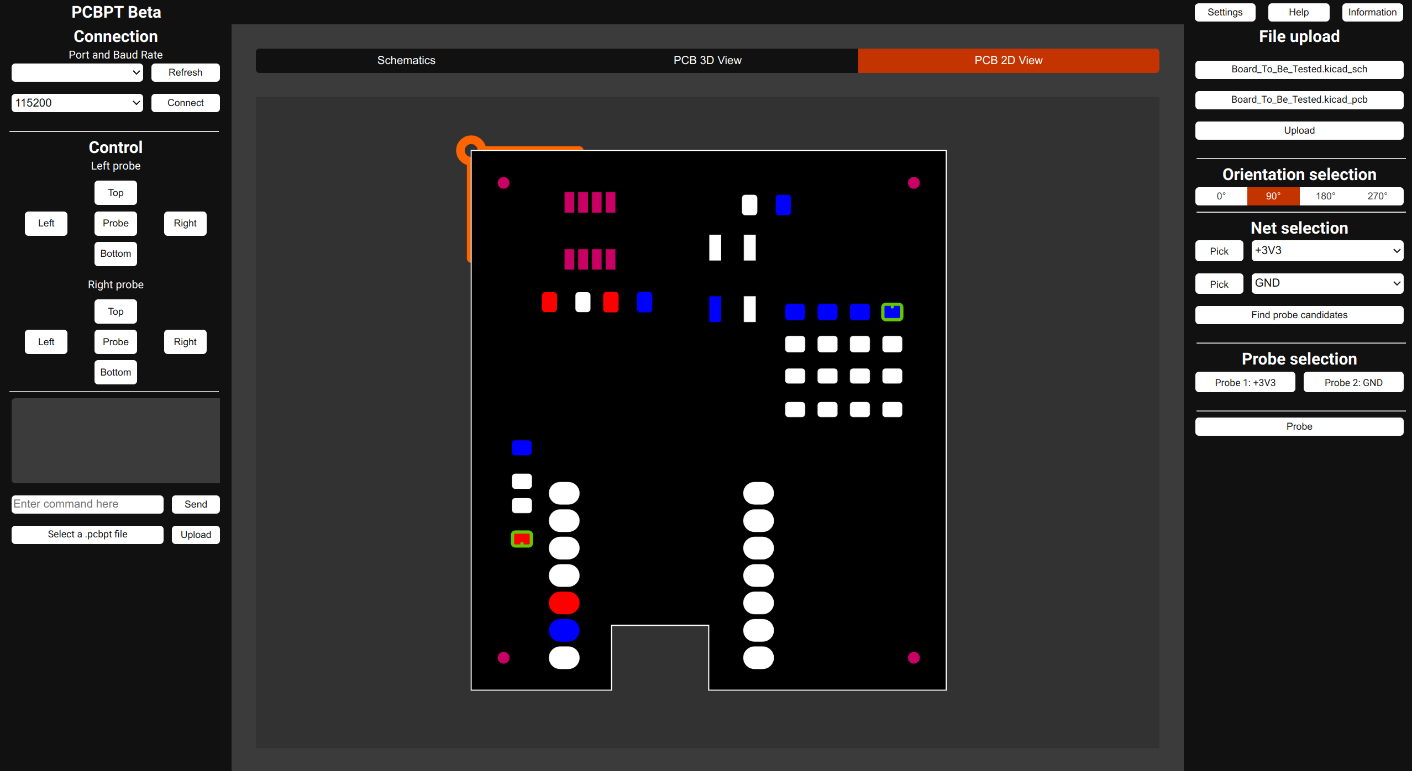
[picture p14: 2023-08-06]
Interface/docs/interface_main_alt.png

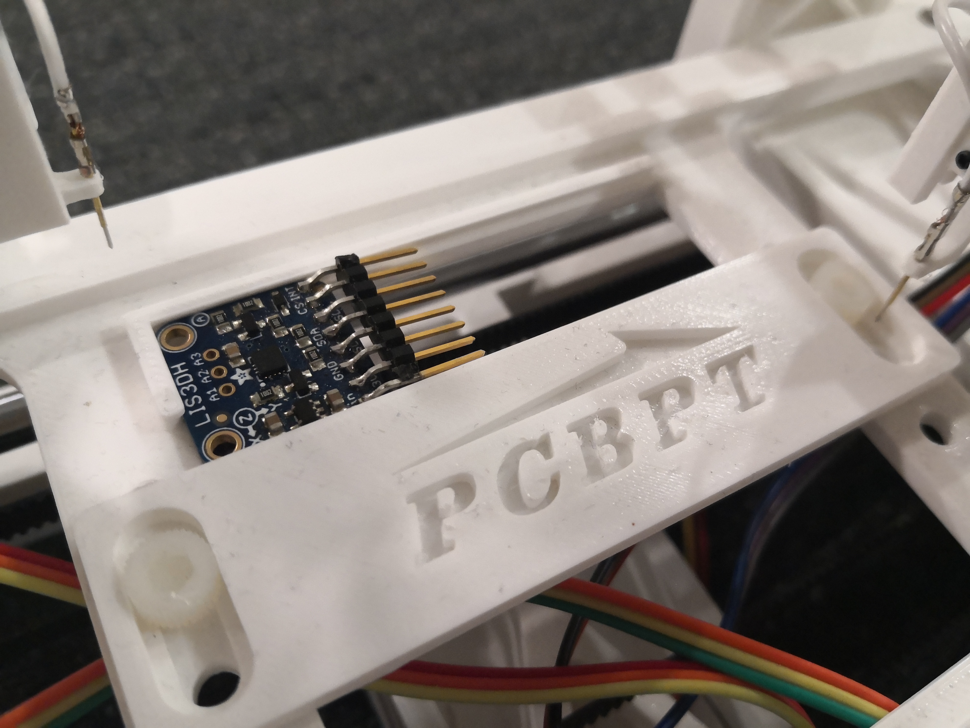
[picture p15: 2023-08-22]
Doc/UIST Demo 2023/TAPs/source/platform_clip_groove.jpg

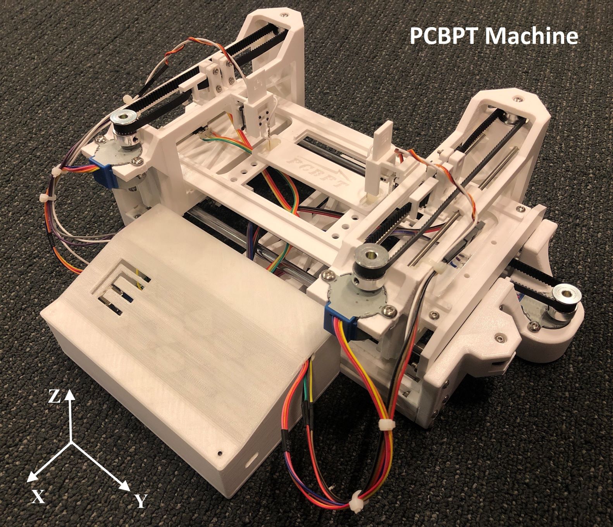
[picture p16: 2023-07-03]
Doc/Tech Briefs/machine copy (1).jpg

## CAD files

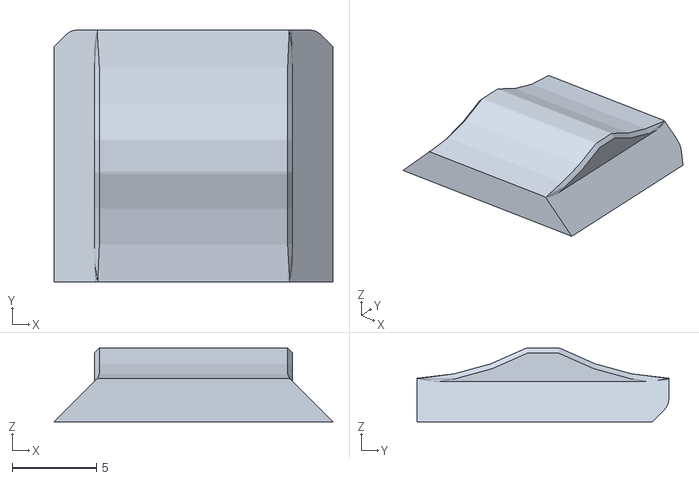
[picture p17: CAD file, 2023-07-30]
Interface/interface/static/models/platform_lock.stl
16.6 x 15.0 x 4.40

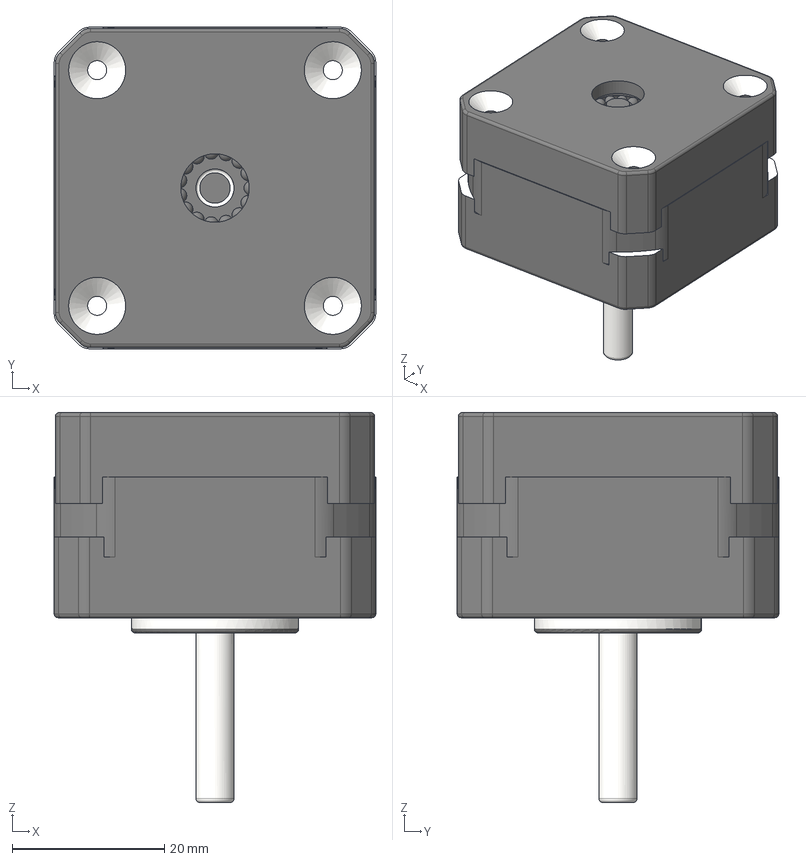
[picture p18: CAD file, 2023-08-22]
PCBPT_V3/Mechanical/Mechanical_1/NEMA_17_PHB42S28-406A v2.step
42.3 x 42.3 x 51.3 mm

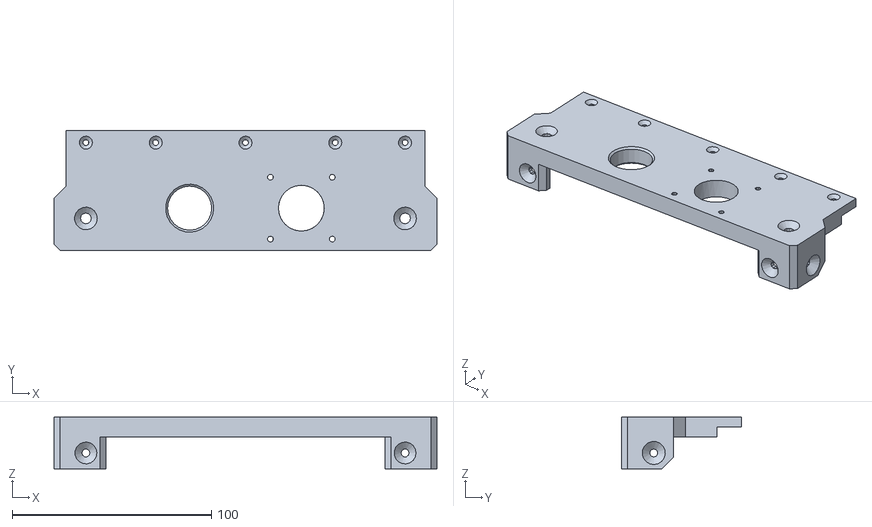
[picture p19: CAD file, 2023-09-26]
PCBPT_V3/Mechanical/Mechanical_1/printings/wall.stl
192.0 x 60.0 x 26.0

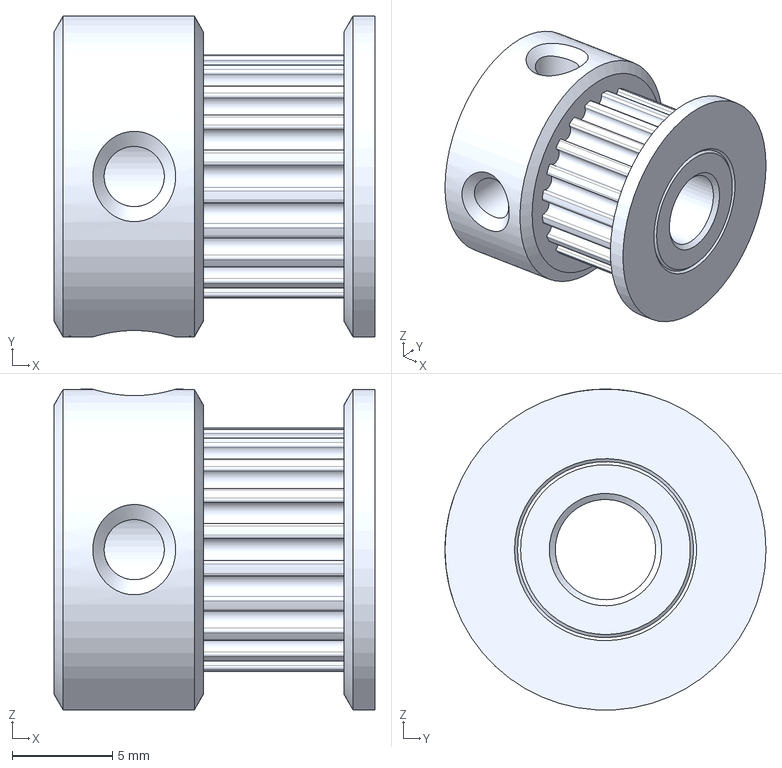
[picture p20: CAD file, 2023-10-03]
PCBPT_V3/Mechanical/Mechanical_2/GT2_motor_pulley.step
16.0 x 16.0 x 16.0 mm

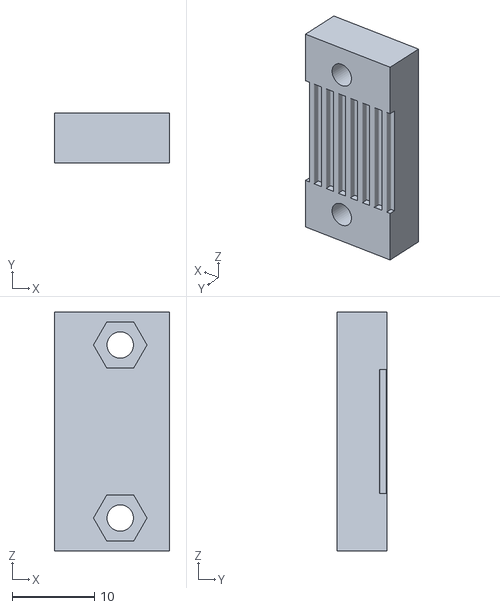
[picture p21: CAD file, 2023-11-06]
PCBPT_V3/Mechanical/Mechanical_2/printings/crane_clamp_holder.STL
14.0 x 6.01 x 29.0

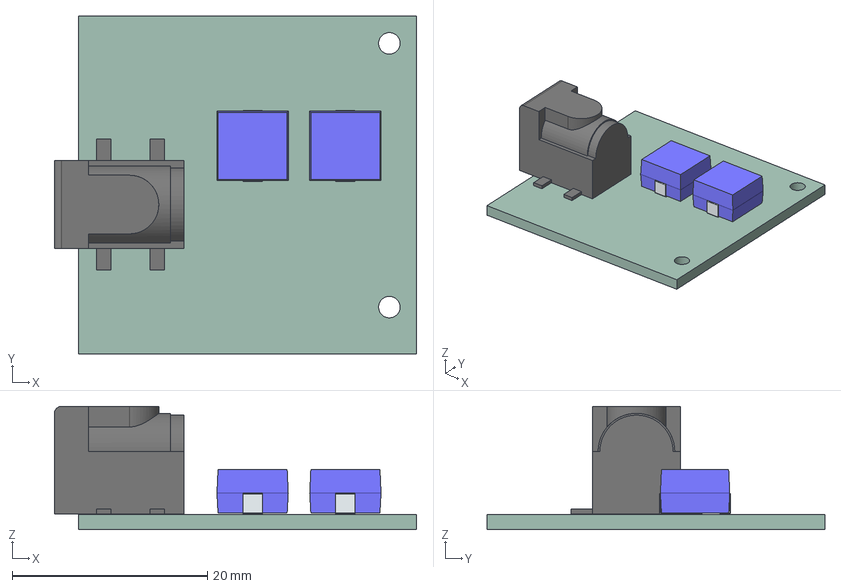
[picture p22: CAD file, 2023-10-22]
PCBPT_V3/PCB/PWR_module/PWR_module_V5.step
37.1 x 34.6 x 12.6 mm
PWR_module PCB

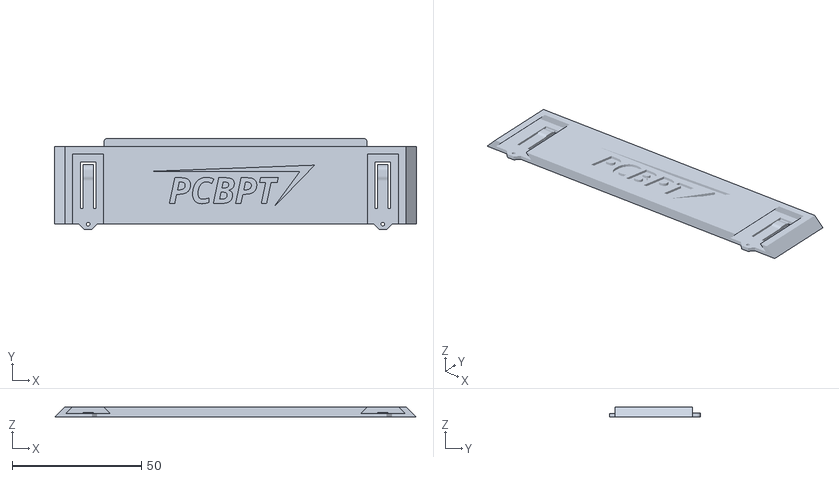
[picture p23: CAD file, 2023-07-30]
Interface/interface/static/models/platform_clip.stl
139.8 x 35.0 x 4.00

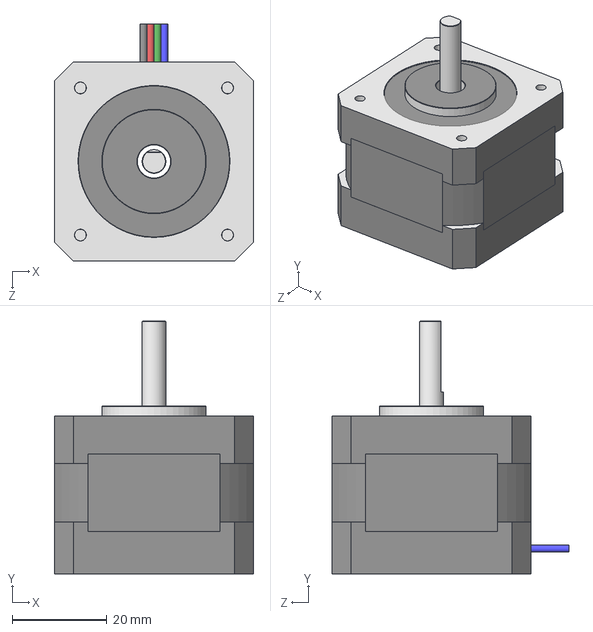
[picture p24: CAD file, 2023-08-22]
PCBPT_V3/Mechanical/Mechanical_1/NEMA17 STEPPER 0.4 A.STEP
42.0 x 53.3 x 50.0 mm

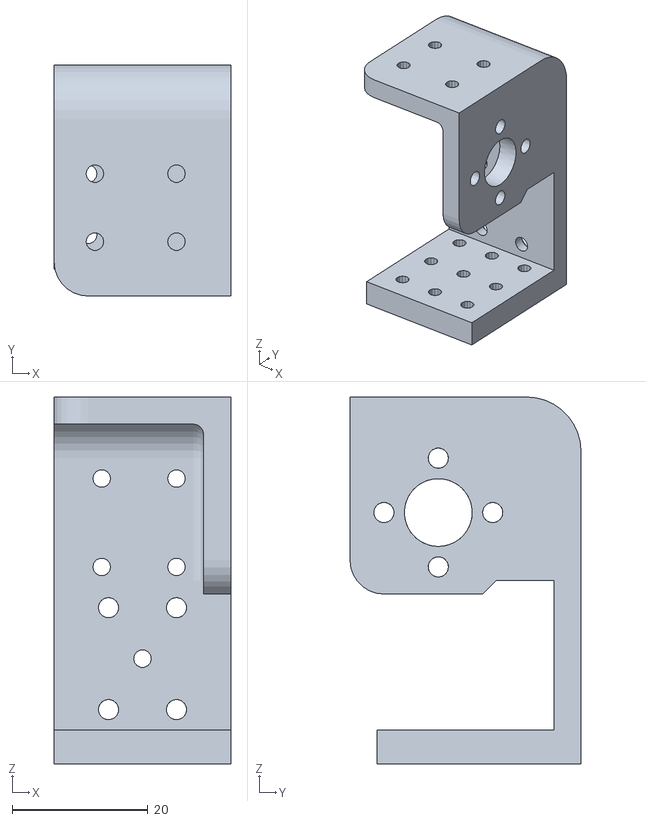
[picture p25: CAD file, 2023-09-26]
PCBPT_V3/Mechanical/Mechanical_1/printings/probe_block_R.stl
26.0 x 34.0 x 54.0

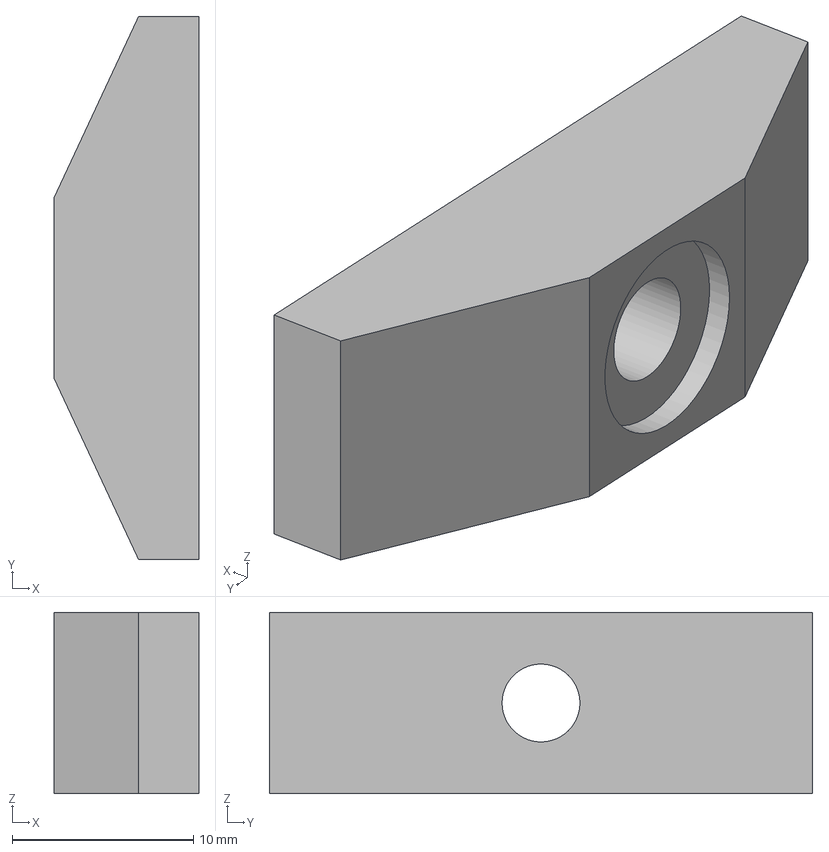
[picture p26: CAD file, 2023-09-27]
PCBPT_V3/Mechanical/Mechanical_2/Part 1 (41).step
8.00 x 30.0 x 10.0 mm

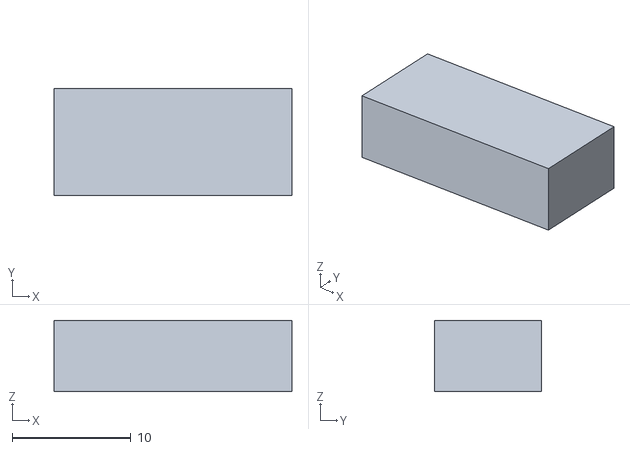
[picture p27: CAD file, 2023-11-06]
PCBPT_V3/Mechanical/Mechanical_2/printings/limit_switch_extention.stl
20.0 x 9.00 x 6.00

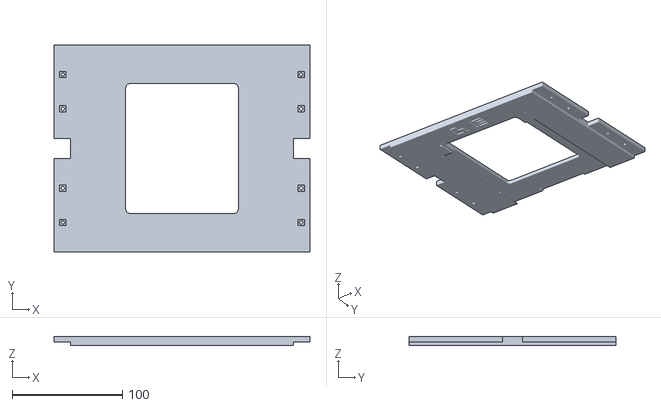
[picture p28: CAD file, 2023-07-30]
Interface/interface/static/models/platform_body.stl
232.0 x 187.8 x 8.00

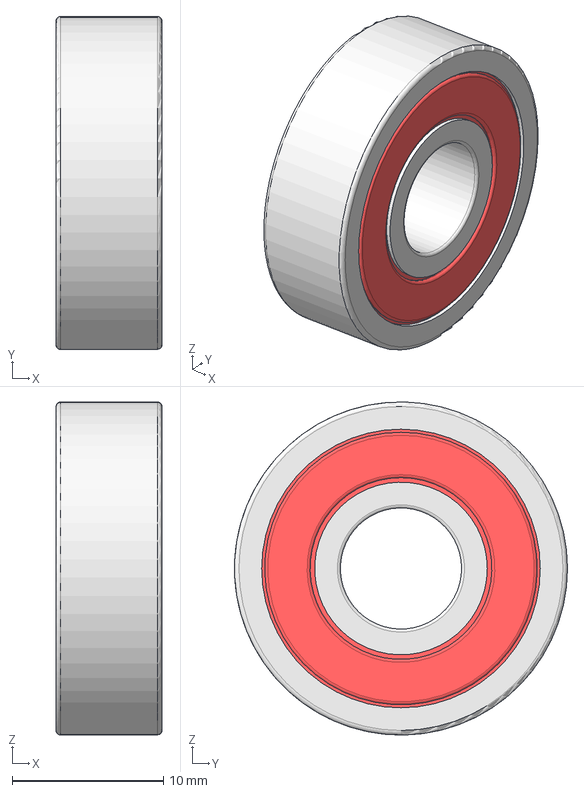
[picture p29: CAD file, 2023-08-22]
PCBPT_V3/Mechanical/Mechanical_1/608-2RS Skate Board Ball Bearing.step
7.00 x 22.0 x 22.0 mm
Ball 001
Ball 002
Ball 003
Ball 004
Ball 005
Ball 006
Ball 007
Outer Ring001
Inner Ring001
Seal 001
Seal 002
Cage 001
Cage clone 002
Rivet 002
Rivet 001
Rivet 007
Rivet 006
Rivet 005
Rivet 004
Rivet 003

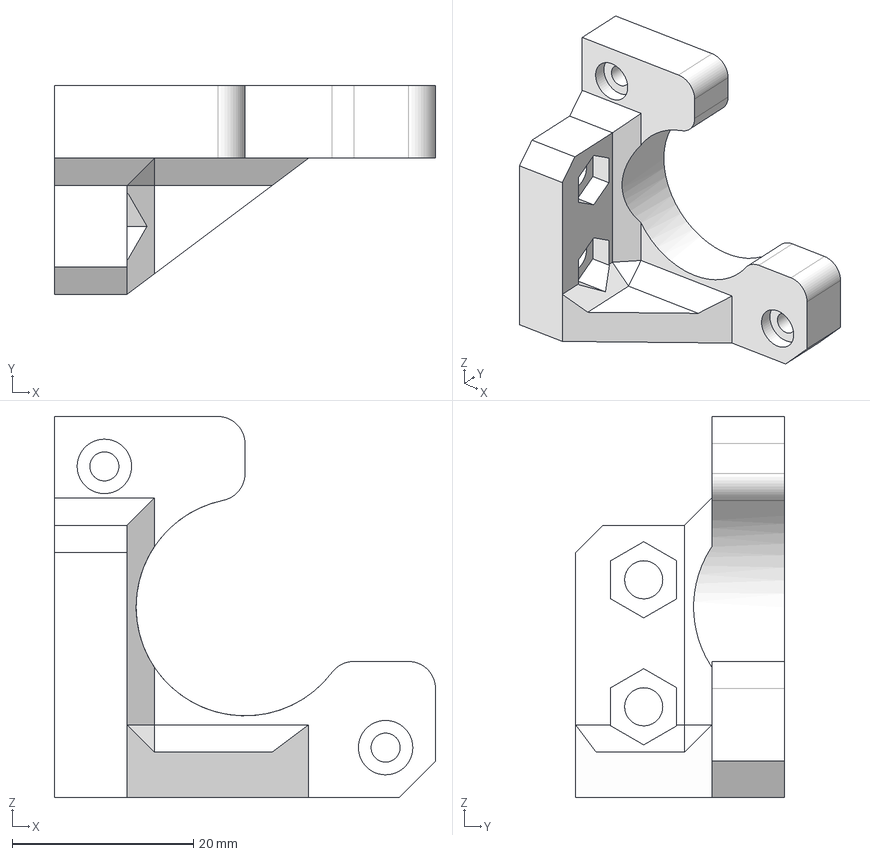
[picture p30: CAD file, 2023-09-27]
PCBPT_V3/Mechanical/Mechanical_2/Part 1 (2).step
42.0 x 23.0 x 42.0 mm

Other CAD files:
PCBPT_V3/Mechanical/Mechanical_1/printings/probe_block_L.stl
PCBPT_V3/Mechanical/Mechanical_2/printings/e_box_lid.stl
PCBPT_V3/Mechanical/Mechanical_1/printings/gantry_R.stl
PCBPT_V3/Mechanical/Mechanical_2/printings/electronic_box.stl
PCBPT_V3/Mechanical/Mechanical_1/2020x260mm.ipt
PCBPT_V3/Mechanical/Mechanical_1/608-2RS Skate Board Ball Bearing/608-2RS Skate Board Ball Bearing.iam
PCBPT_V3/Mechanical/Mechanical_1/608-2RS Skate Board Ball Bearing/Ball 001.ipt
PCBPT_V3/Mechanical/Mechanical_1/608-2RS Skate Board Ball Bearing/Ball 002.ipt
PCBPT_V3/Mechanical/Mechanical_1/608-2RS Skate Board Ball Bearing/Ball 003.ipt
PCBPT_V3/Mechanical/Mechanical_1/608-2RS Skate Board Ball Bearing/Ball 004.ipt
PCBPT_V3/Mechanical/Mechanical_1/608-2RS Skate Board Ball Bearing/Ball 005.ipt
PCBPT_V3/Mechanical/Mechanical_1/608-2RS Skate Board Ball Bearing/Ball 006.ipt
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

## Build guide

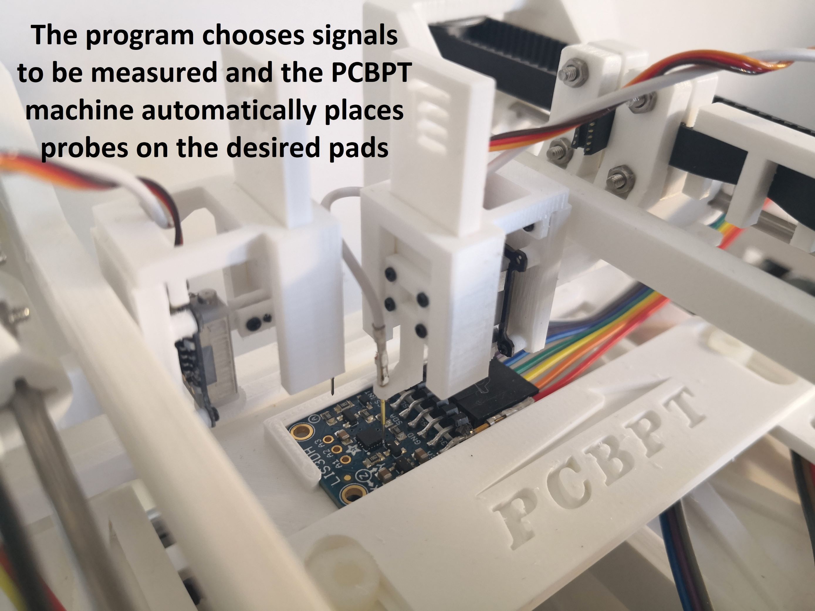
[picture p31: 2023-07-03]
Doc/Tech Briefs/platform_install_pcb (1).jpg

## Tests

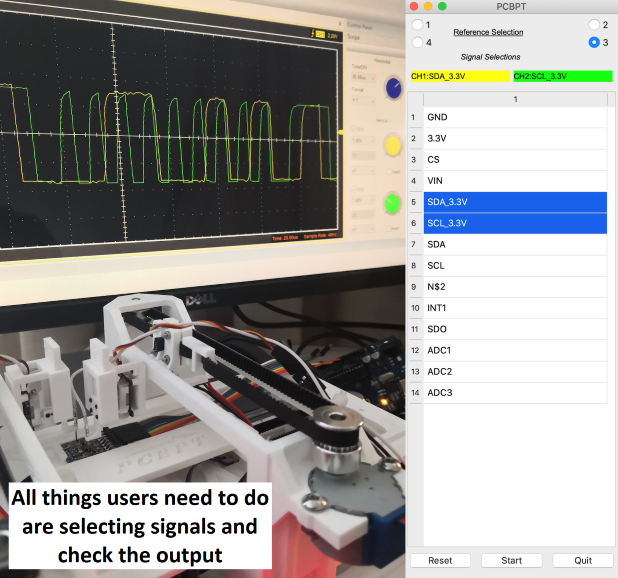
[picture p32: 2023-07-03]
Doc/Tech Briefs/result (1).png

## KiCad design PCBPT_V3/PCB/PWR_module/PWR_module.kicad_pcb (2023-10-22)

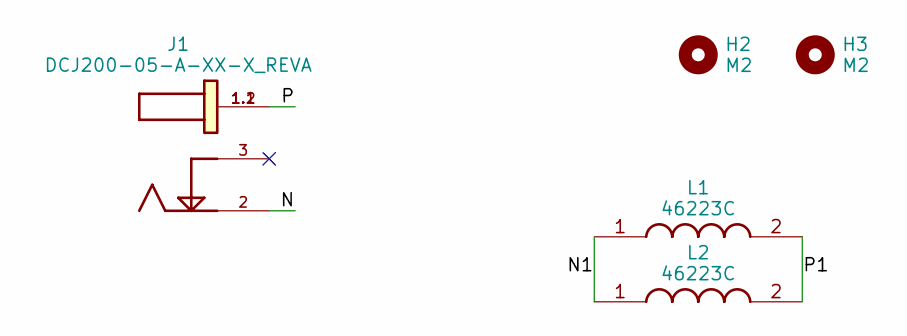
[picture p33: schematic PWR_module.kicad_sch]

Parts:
H2, H3: M2; MountingHole_2.2mm_M2
J1: DCJ200-05-A-XX-X_REVA; GCT_DCJ200-05-A-XX-X_REVA
L1, L2: 46223C; INDPM7373X455N; Mouser Part Number 580-46223C

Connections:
/N: J1.2
/N1: L1.1, L2.1
/P: J1.1.1, J1.1.2
/P1: L1.2, L2.2

Board: 2 copper layers, 5 parts (0 on the bottom side), 3 nets, no tracks yet.

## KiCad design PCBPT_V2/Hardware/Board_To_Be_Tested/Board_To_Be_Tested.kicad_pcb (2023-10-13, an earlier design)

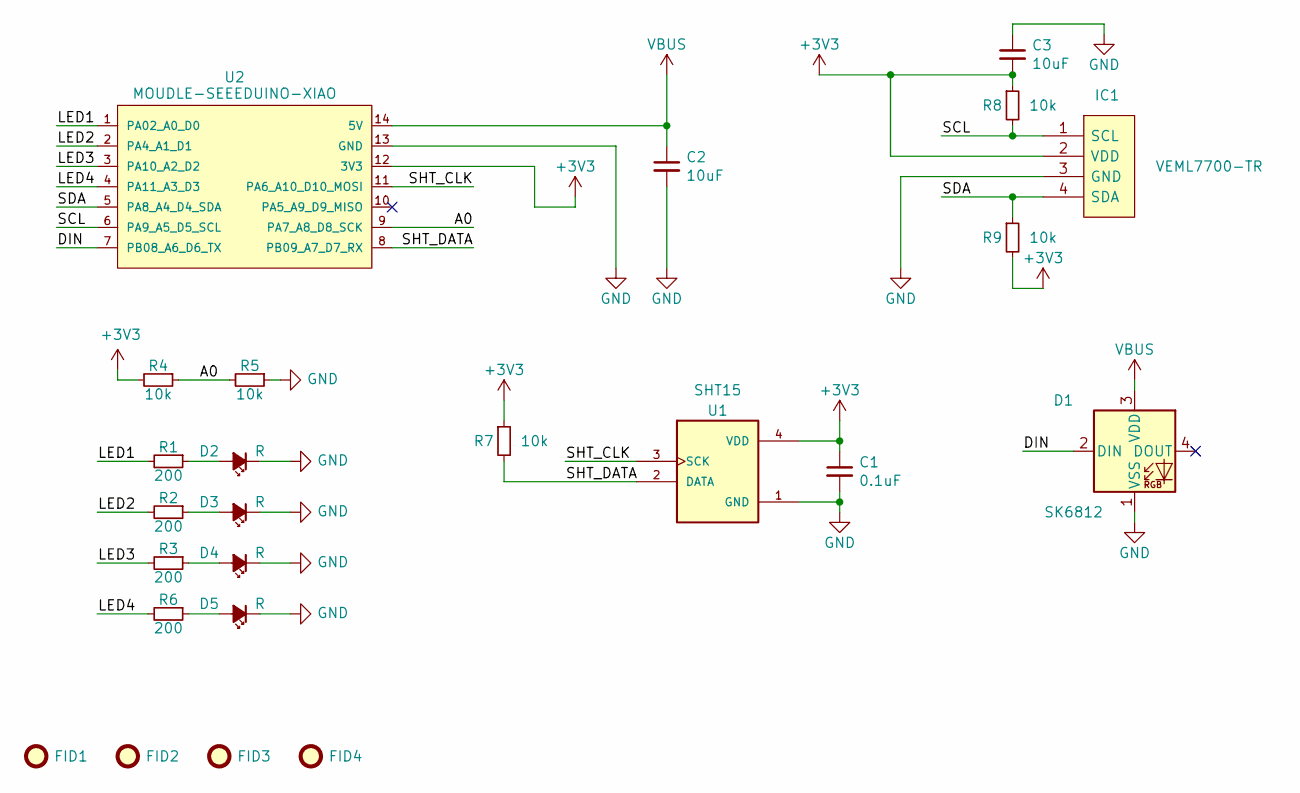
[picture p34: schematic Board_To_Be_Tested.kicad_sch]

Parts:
C1: 0.1uF; C_1206_3216Metric_Pad1.33x1.80mm_HandSolder
C2, C3: 10uF; C_1206_3216Metric_Pad1.33x1.80mm_HandSolder
D1: SK6812; LED_SK6812_PLCC4_5.0x5.0mm_P3.2mm
D2, D3, D4, D5: R; LED_1206_3216Metric_Pad1.42x1.75mm_HandSolder
FID1, FID2, FID3, FID4: Fiducial; Fiducial_1mm_Mask2mm
IC1: VEML7700-TR; VEML7700; Manufacturer_Part_Number VEML7700-TR; Mouser Part Number 78-VEML7700-TR
R1, R2, R3, R6: 200; R_1206_3216Metric_Pad1.30x1.75mm_HandSolder
R4, R5, R7, R8, R9: 10k; R_1206_3216Metric_Pad1.30x1.75mm_HandSolder
U1: SHT15; DFN747X493X250-8N
U2: MOUDLE-SEEEDUINO-XIAO; MOUDLE14P-SMD-2.54-21X17.8MM

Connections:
+3V3: C1.1, C3.2, IC1.2 (VDD), R4.2, R7.1, R8.1, R9.2, U1.4 (VDD), U2.12 (3V3)
/A0: R4.1, R5.2, U2.9 (PA7_A8_D8_SCK)
/DIN: D1.2 (DIN), U2.7 (PB08_A6_D6_TX)
/LED1: R1.2, U2.1 (PA02_A0_D0)
/LED2: R2.2, U2.2 (PA4_A1_D1)
/LED3: R3.2, U2.3 (PA10_A2_D2)
/LED4: R6.2, U2.4 (PA11_A3_D3)
/SCL: IC1.1 (SCL), R8.2, U2.6 (PA9_A5_D5_SCL)
/SDA: IC1.4 (SDA), R9.1, U2.5 (PA8_A4_D4_SDA)
/SHT_CLK: U1.3 (SCK), U2.11 (PA6_A10_D10_MOSI)
/SHT_DATA: R7.2, U1.2 (DATA), U2.8 (PB09_A7_D7_RX)
GND: C1.2, C2.2, C3.1, D1.1 (VSS), D2.1 (K), D3.1 (K), D4.1 (K), D5.1 (K), IC1.3 (GND), R5.1, U1.1 (GND), U2.13 (GND)
unnamed: D2.2 (A), R1.1
unnamed: D3.2 (A), R2.1
unnamed: D4.2 (A), R3.1
unnamed: D5.2 (A), R6.1
VBUS: C2.1, D1.3 (VDD), U2.14 (5V)

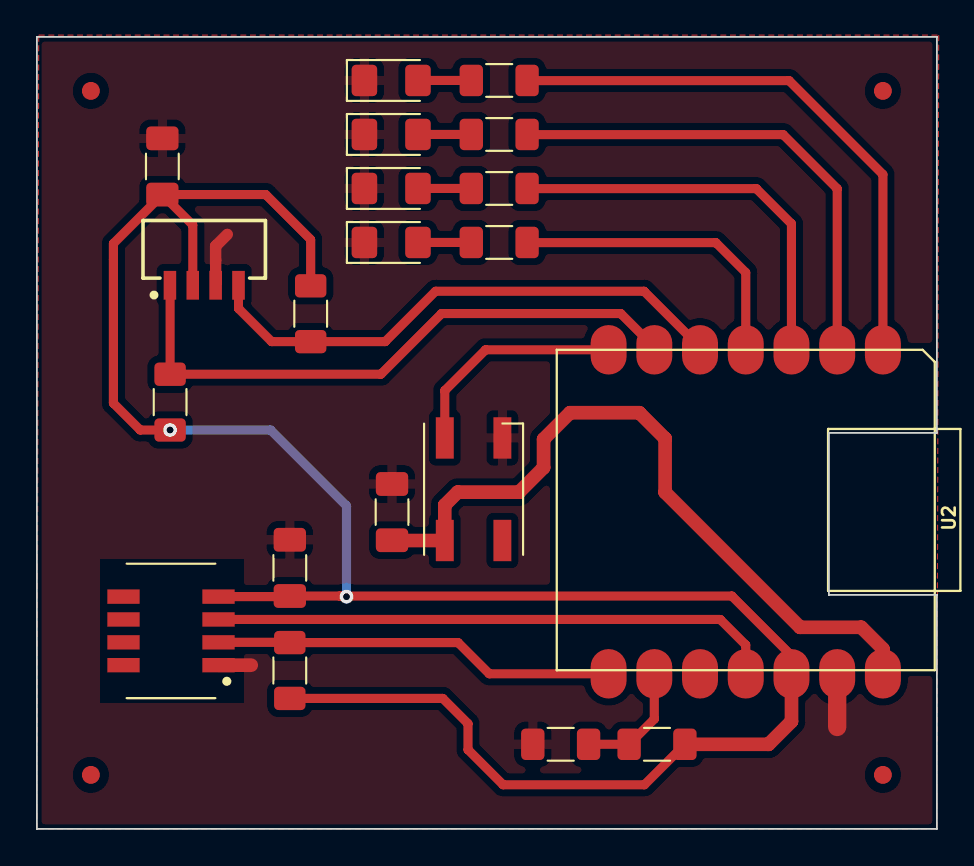
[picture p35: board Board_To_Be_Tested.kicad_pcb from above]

Board: 2 copper layers, 50.0 x 44.0 mm, 24 parts (0 on the bottom side), 17 nets.

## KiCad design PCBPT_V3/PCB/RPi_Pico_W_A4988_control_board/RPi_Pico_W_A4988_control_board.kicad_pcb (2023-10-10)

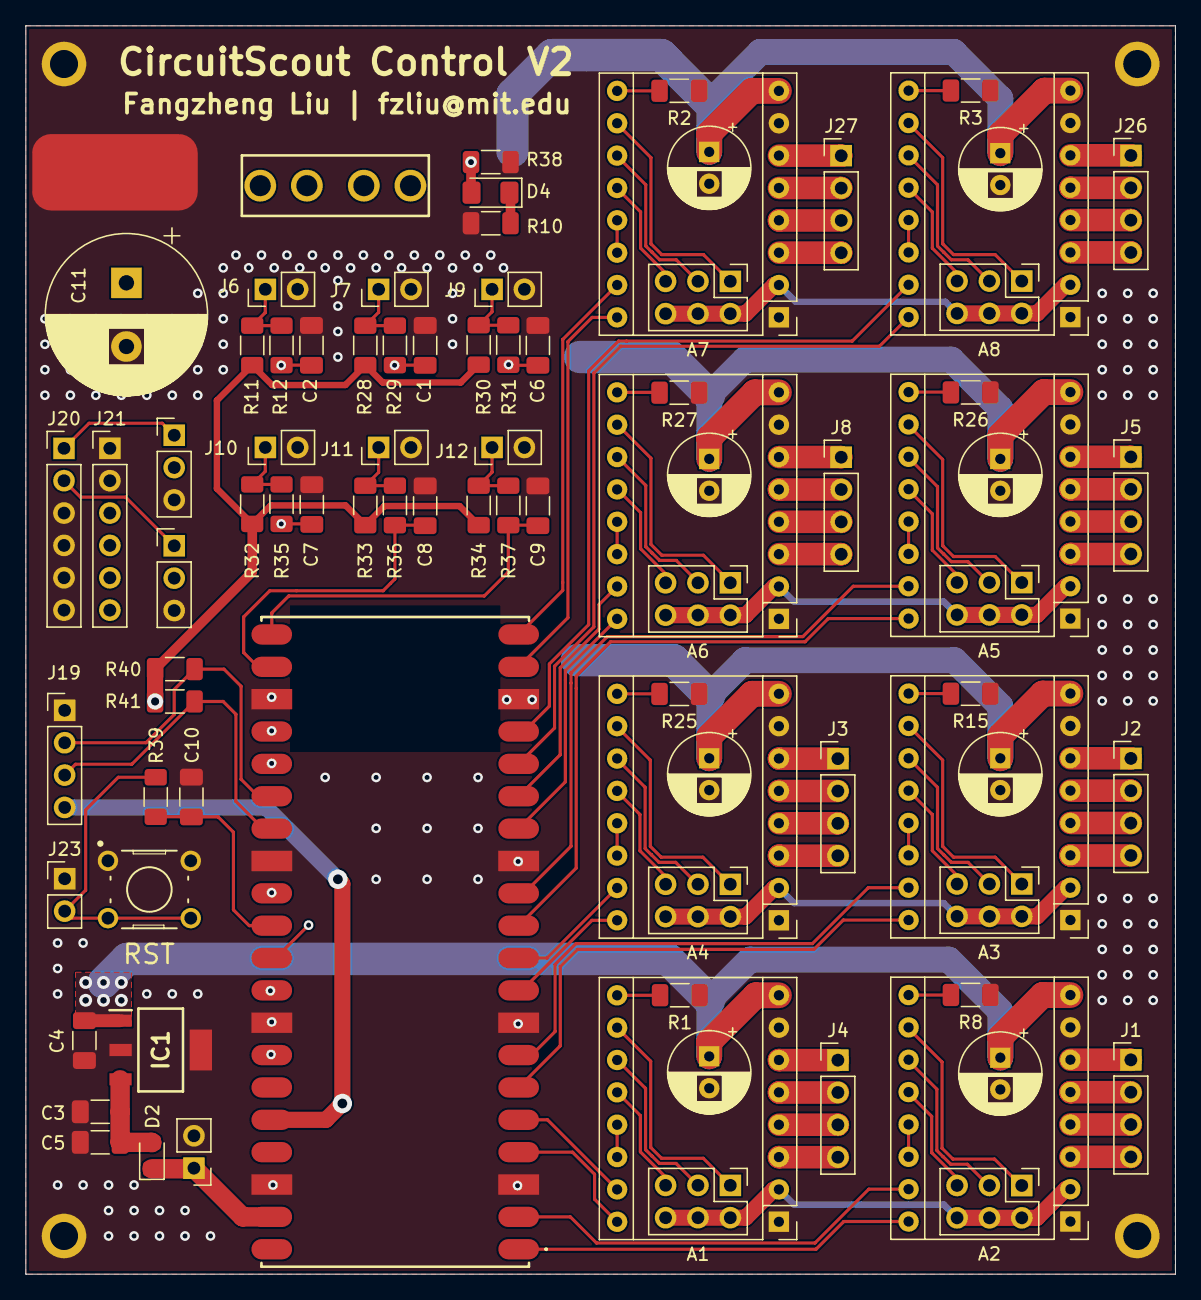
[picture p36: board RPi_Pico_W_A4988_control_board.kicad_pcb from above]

Board: 4 copper layers, 90.2 x 98.0 mm, 93 parts (1 on the bottom side), 113 nets.

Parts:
A1, A2, A3, A4, A5, A6, A7, A8: Pololu_Breakout_A4988; Pololu_Breakout-16_15.2x20.3mm
C1, C2, C6, C7, C8, C9, C10: 0.01uF; C_1206_3216Metric_Pad1.33x1.80mm_HandSolder
C3: 22uF; C_1206_3216Metric_Pad1.33x1.80mm_HandSolder
C4: 0.47uF; C_1206_3216Metric_Pad1.33x1.80mm_HandSolder
C5: 0.1uF; C_1206_3216Metric_Pad1.33x1.80mm_HandSolder
C11: 470uF; CP_Radial_D12.5mm_P5.00mm
C12, C13, C14, C15, C16, C17, C18, C19: 100uF; CP_Radial_D6.3mm_P2.50mm
D2: Schottky; D_0805_2012Metric_Pad1.15x1.40mm_HandSolder
D4: LED_Small_Filled; LED_1206_3216Metric_Pad1.42x1.75mm_HandSolder
H1, H2, H3, H4: M2; MountingHole_2.2mm_M2_ISO7380_Pad
IC1: UA78M05IDCYR; SOT230P700X180-4N
IC2: RASPBERRY_PI_PICO_W; RASPBERRYPIPICOW
J1, J2, J3, J4, J5, J8, J19, J26, J27: Limit Switch; PinHeader_1x04_P2.54mm_Vertical
J6, J7, J9, J10, J11, J12, J22, J23: Limit Switch; PinHeader_1x02_P2.54mm_Vertical
J13, J14, J15, J16, J17, J18, J24, J25: Conn_02x03_Odd_Even; PinHeader_2x03_P2.54mm_Vertical
J20, J21: Conn_01x06_Pin; PinHeader_1x06_P2.54mm_Vertical
J28, J29: Conn_01x03_Pin; PinHeader_1x03_P2.54mm_Vertical
J30, J31: pin; conn_SMD_15mmx5mm
R1, R2, R3, R8, R11, R15, R25, R26, R27, R28, R30, R32, R33, R34, R40, R41: 10K; R_1206_3216Metric_Pad1.30x1.75mm_HandSolder
R10: 10k; R_1206_3216Metric_Pad1.30x1.75mm_HandSolder
R12, R29, R31, R35, R36, R37, R39: 100; R_1206_3216Metric_Pad1.30x1.75mm_HandSolder
R38: 100K; R_1206_3216Metric_Pad1.30x1.75mm_HandSolder
SW1: SW_MEC_5E; SW_B3F-1000
U1: 3544-2

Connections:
1A_1: A1.4 (1A), J4.3
1A_2: A2.4 (1A), J1.3
1A_3: A3.4 (1A), J2.3
1A_4: A4.4 (1A), J3.3
1A_5: A5.4 (1A), J5.3
1A_6: A6.4 (1A), J8.3
1A_7: A7.4 (1A), J27.3
1A_8: A8.4 (1A), J26.3
1B_1: A1.3 (1B), J4.4
1B_2: A2.3 (1B), J1.4
1B_3: A3.3 (1B), J2.4
1B_4: A4.3 (1B), J3.4
1B_5: A5.3 (1B), J5.4
1B_6: A6.3 (1B), J8.4
1B_7: A7.3 (1B), J27.4
1B_8: A8.3 (1B), J26.4
2A_1: A1.5 (2A), J4.2
2A_2: A2.5 (2A), J1.2
2A_3: A3.5 (2A), J2.2
2A_4: A4.5 (2A), J3.2
2A_5: A5.5 (2A), J5.2
2A_6: A6.5 (2A), J8.2
2A_7: A7.5 (2A), J27.2
2A_8: A8.5 (2A), J26.2
2B_1: A1.6 (2B), J4.1
2B_2: A2.6 (2B), J1.1
2B_3: A3.6 (2B), J2.1
2B_4: A4.6 (2B), J3.1
2B_5: A5.6 (2B), J5.1
2B_6: A6.6 (2B), J8.1
2B_7: A7.6 (2B), J27.1
2B_8: A8.6 (2B), J26.1
+3V3: A1.2 (VDD), A2.2 (VDD), A3.2 (VDD), A4.2 (VDD), A5.2 (VDD), A6.2 (VDD), A7.2 (VDD), A8.2 (VDD), IC2.36 (3V3(OUT)), J13.2, J13.4, J13.6, J14.2, J14.4, J14.6, J15.2, J15.4, J15.6, J16.2, J16.4, J16.6, J17.2, J17.4, J17.6, J18.2, J18.4, J18.6, J19.4, J21.5, J21.6, J24.2, J24.4, J24.6, J25.2, J25.4, J25.6, R11.1, R28.1, R30.1, R32.1, R33.1, R34.1, R40.1, R41.1
+5V: C3.1, C5.1, D2.2 (A), IC1.3 (OUT)
+12V: C11.1, J30.1, U1.1, U1.2
/PicoW RP2040/~RST: C10.1, IC2.30 (RUN), R39.1
DIR_1: A1.16 (DIR), IC2.4 (I2C1_SDA_/SPI0_SCK/GP2)
DIR_2: A2.16 (DIR), IC2.1 (UART0_TX/I2C0_SDA_/SPI0_RX/GP0)
DIR_3: A3.16 (DIR), IC2.6 (UART1_TX/I2C0_SDA_/SPI0_RX/GP4)
DIR_4: A4.16 (DIR), IC2.9 (I2C1_SDA_/SPI0_SCK/GP6)
DIR_5: A5.16 (DIR), IC2.11 (UART1_TX/I2C0_SDA_/SPI1_RX/GP8)
DIR_6: A6.16 (DIR), IC2.14 (I2C1_SDA_/SPI1__SCK/GP10)
DIR_7: A7.16 (DIR), IC2.19 (I2C1_SDA/SPI1_SCK/GP14)
DIR_8: A8.16 (DIR), IC2.16 (UART0_TX/I2C0_SDA_/SPI1_RX_/GP12)
GND: A1.1 (GND), A1.7 (GND), A2.1 (GND), A2.7 (GND), A3.1 (GND), A3.7 (GND), A4.1 (GND), A4.7 (GND), A5.1 (GND), A5.7 (GND), A6.1 (GND), A6.7 (GND), A7.1 (GND), A7.7 (GND), A8.1 (GND), A8.7 (GND), C1.2, C2.2, C3.2, C4.2, C5.2, C6.2, C7.2, C8.2, C9.2, C10.2, C11.2, C12.2, C13.2, C14.2, C15.2, C16.2, C17.2, C18.2, C19.2, H1.1, H2.1, H3.1, H4.1, IC1.2 (GND_1), IC1.4 (GND_2), IC2.3 (GND_1), IC2.8 (GND_2), IC2.13 (GND_3), IC2.18 (GND_4), IC2.23 (GND_5), IC2.28 (GND_6), IC2.33 (GND/AGND), IC2.38 (GND_7), J6.2, J7.2, J9.2, J10.2, J11.2, J12.2, J19.1, J20.3, J20.4, J20.5, J20.6, J21.1, J21.2, J22.2, J23.1, J28.3, J29.3, J31.1, R1.2, R2.2, R3.2, R8.2, R10.2, R15.2, R25.2, R26.2, R27.2, R38.2, SW1.1, SW1.2
IO27: IC2.32 (I2C1_SCL_/ADC1/GP_27), J20.1, J28.1
IO28: IC2.34 (GP28/ADC2), J20.2, J29.1
LIMIT_SW_1: C2.1, IC2.29 (GP22), R12.1
LIMIT_SW_2: C1.1, IC2.25 (I2C1_SCL/_SPI0_TX/GP19), R29.1
LIMIT_SW_3: C6.1, IC2.24 (I2C1_SDA/_SPI0_SCK/GP18), R31.1
LIMIT_SW_4: C7.1, IC2.31 (I2C1_SDA/ADC0/GP26), R35.1
LIMIT_SW_5: C8.1, IC2.22 (UART0_RX/I2C0_SCL/SPIO_CSN/GP17), R36.1
LIMIT_SW_6: C9.1, IC2.21 (UART0_TX/I2C0_SDA_/SPI0_RX_/GP16), R37.1
MS1_1: A1.10 (MS1), J13.1
MS1_2: A2.10 (MS1), J14.1
MS1_3: A3.10 (MS1), J15.1
MS1_4: A4.10 (MS1), J16.1
MS1_5: A5.10 (MS1), J17.1
MS1_6: A6.10 (MS1), J18.1
MS1_7: A7.10 (MS1), J24.1
MS1_8: A8.10 (MS1), J25.1
MS2_1: A1.11 (MS2), J13.3
MS2_2: A2.11 (MS2), J14.3
MS2_3: A3.11 (MS2), J15.3
MS2_4: A4.11 (MS2), J16.3
MS2_5: A5.11 (MS2), J17.3
MS2_6: A6.11 (MS2), J18.3
MS2_7: A7.11 (MS2), J24.3
MS2_8: A8.11 (MS2), J25.3
MS3_1: A1.12 (MS3), J13.5
MS3_2: A2.12 (MS3), J14.5
MS3_3: A3.12 (MS3), J15.5
MS3_4: A4.12 (MS3), J16.5
MS3_5: A5.12 (MS3), J17.5
MS3_6: A6.12 (MS3), J18.5
MS3_7: A7.12 (MS3), J24.5
MS3_8: A8.12 (MS3), J25.5
unnamed: A1.9 (~ENABLE), R1.1
unnamed: A1.13 (~RESET), A1.14 (~SLEEP)
unnamed: A2.9 (~ENABLE), R8.1
unnamed: A2.13 (~RESET), A2.14 (~SLEEP)
unnamed: A3.9 (~ENABLE), R15.1
unnamed: A3.13 (~RESET), A3.14 (~SLEEP)
unnamed: A4.9 (~ENABLE), R25.1
unnamed: A4.13 (~RESET), A4.14 (~SLEEP)
unnamed: A5.9 (~ENABLE), R26.1
unnamed: A5.13 (~RESET), A5.14 (~SLEEP)
unnamed: A6.9 (~ENABLE), R27.1
unnamed: A6.13 (~RESET), A6.14 (~SLEEP)
unnamed: A7.9 (~ENABLE), R2.1
unnamed: A7.13 (~RESET), A7.14 (~SLEEP)
unnamed: A8.9 (~ENABLE), R3.1
unnamed: A8.13 (~RESET), A8.14 (~SLEEP)
unnamed: D4.1 (K), R10.1
unnamed: J6.1, R11.2, R12.2
unnamed: J7.1, R28.2, R29.2
unnamed: J9.1, R30.2, R31.2
unnamed: J10.1, R32.2, R35.2
unnamed: J11.1, R33.2, R36.2
unnamed: J12.1, R34.2, R37.2
unnamed: J23.2, R39.2, SW1.3 (K), SW1.4 (A)
SCL: IC2.27 (I2C0_SCL/GP21), J19.3, R41.2
SDA: IC2.26 (I2C0_SDA/GP20), J19.2, R40.2
STEP_1: A1.15 (STEP), IC2.5 (I2C0_SCL_/SPI0_TX/GP3)
STEP_2: A2.15 (STEP), IC2.2 (UART0_RX/I2C0_SCL_/SPI0_CSN/GP1)
STEP_3: A3.15 (STEP), IC2.7 (UART1_RX/I2C0_SCL_/SPI0_CSN/GP5)
STEP_4: A4.15 (STEP), IC2.10 (I2C1_SCL_/SPI0_TX/GP7)
STEP_5: A5.15 (STEP), IC2.12 (UART1_RX/I2C0_SCL_/SPI1_CSN/GP9)
STEP_6: A6.15 (STEP), IC2.15 (I2C1_SCL_/SPI1__TX/GP11)
STEP_7: A7.15 (STEP), IC2.20 (I2C1_SCL/SPI1_TX/GP15)
STEP_8: A8.15 (STEP), IC2.17 (UART0_RX/I2C0_SCL_/SPI1_CSN/GP13)
VPP: A1.8 (VMOT), A2.8 (VMOT), A3.8 (VMOT), A4.8 (VMOT), A5.8 (VMOT), A6.8 (VMOT), A7.8 (VMOT), A8.8 (VMOT), C4.1, C12.1, C13.1, C14.1, C15.1, C16.1, C17.1, C18.1, C19.1, D4.2 (A), IC1.1 (IN), R38.1, U1.3, U1.4
VSYS: D2.1 (K), IC2.39 (VSYS), J21.3, J21.4, J22.1, J28.2, J29.2

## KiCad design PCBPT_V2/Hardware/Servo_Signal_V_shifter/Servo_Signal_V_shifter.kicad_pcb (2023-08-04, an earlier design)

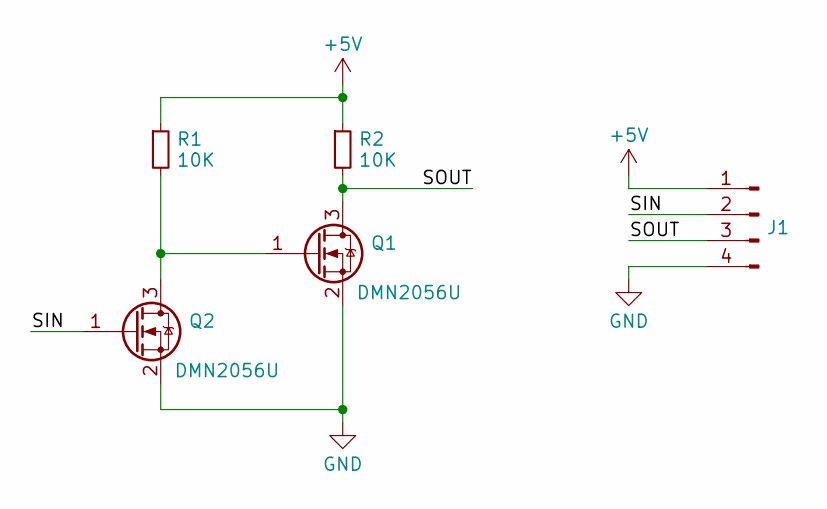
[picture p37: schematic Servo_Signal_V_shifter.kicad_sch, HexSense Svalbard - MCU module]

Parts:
J1: Conn_01x04_Pin; Harwin_M20-89004xx_1x04_P2.54mm_Horizontal
Q1, Q2: DMN2056U; SOT-23
R1, R2: 10K; R_1206_3216Metric_Pad1.30x1.75mm_HandSolder

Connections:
+5V: J1.1, R1.1, R2.1
/SIN: J1.2, Q2.1 (G)
/SOUT: J1.3, Q1.3 (D), R2.2
GND: J1.4, Q1.2 (S), Q2.2 (S)
unnamed: Q1.1 (G), Q2.3 (D), R1.2

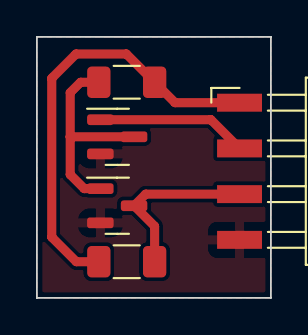
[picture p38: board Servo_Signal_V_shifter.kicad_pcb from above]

Board: 2 copper layers, 13.0 x 14.5 mm, 5 parts (0 on the bottom side), 5 nets.

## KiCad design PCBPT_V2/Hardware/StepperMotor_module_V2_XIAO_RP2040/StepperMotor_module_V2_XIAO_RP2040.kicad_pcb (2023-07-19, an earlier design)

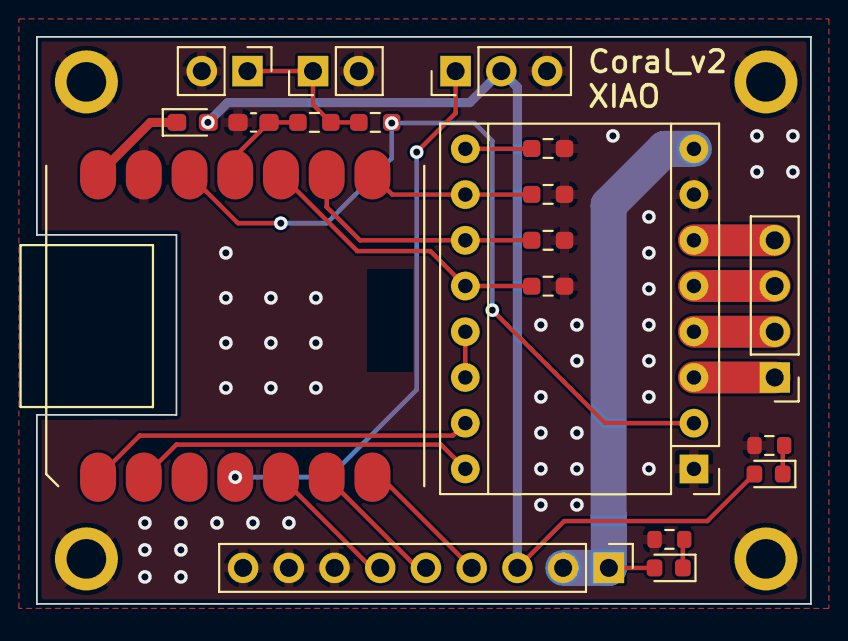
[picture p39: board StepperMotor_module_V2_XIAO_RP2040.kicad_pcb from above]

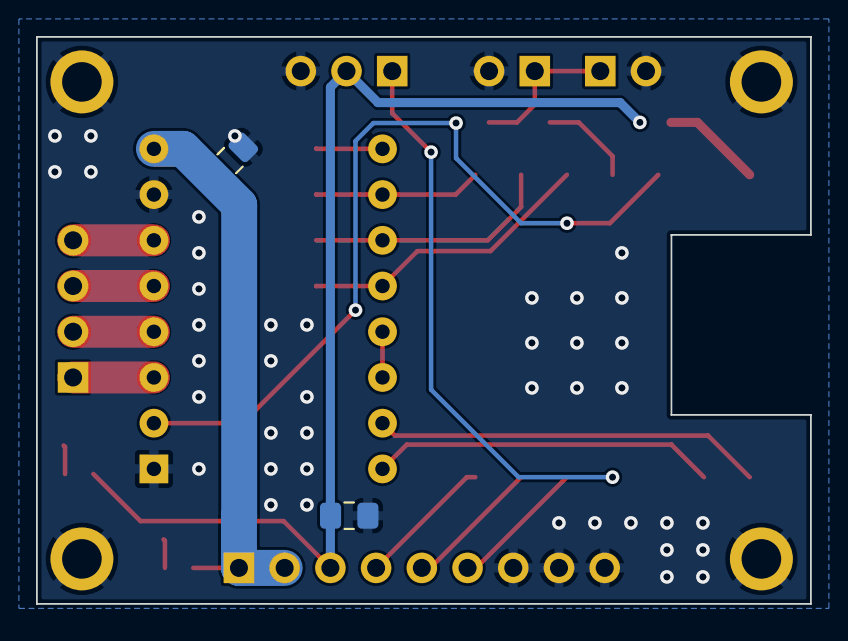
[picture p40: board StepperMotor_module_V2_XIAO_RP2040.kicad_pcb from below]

Board: 2 copper layers, 43.0 x 31.5 mm, 25 parts (2 on the bottom side), 24 nets.

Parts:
A1: Pololu_Breakout_A4988; Pololu_Breakout-16_15.2x20.3mm
C1, C3: 0.1uF; C_0805_2012Metric_Pad1.18x1.45mm_HandSolder
C2: 0.01uF; C_0603_1608Metric_Pad1.08x0.95mm_HandSolder
D1, D4: LED_Small_Filled; LED_0603_1608Metric
D2: Schottky; D_0603_1608Metric_Pad1.05x0.95mm_HandSolder
H1, H2, H3, H4: M2; MountingHole_2.2mm_M2_ISO7380_Pad
J3: Servo; PinHeader_1x03_P2.54mm_Vertical
J4: Limit Switch; PinHeader_1x04_P2.54mm_Vertical
J5: Conn_01x09_Pin; PinHeader_1x09_P2.54mm_Vertical
J6, J7: Limit Switch; PinHeader_1x02_P2.54mm_Vertical
R1: 499K; R_0603_1608Metric_Pad0.98x0.95mm_HandSolder
R2, R3, R4, R11: 10K; R_0603_1608Metric_Pad0.98x0.95mm_HandSolder
R8, R10: 10k; R_0603_1608Metric
R12: 100; R_0603_1608Metric_Pad0.98x0.95mm_HandSolder
U1: MOUDLE-SEEEDUINO-XIAO; MOUDLE14P-SMD-2.54-21X17.8MM

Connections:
1A: A1.4 (1A), J4.2
1B: A1.3 (1B), J4.1
2A: A1.5 (2A), J4.3
2B: A1.6 (2B), J4.4
+3V3: A1.2 (VDD), R11.1, U1.12 (3V3)
/A4988_Module/M_EN: A1.9 (~ENABLE), R1.1
DIR: A1.16 (DIR), U1.2 (PA4_A1_D1)
GND: A1.1 (GND), A1.7 (GND), C1.2, C2.2, C3.2, H1.1, H2.1, H3.1, H4.1, J3.3, J5.7, J5.8, J5.9, J6.2, J7.2, R1.2, R2.2, R3.2, R4.2, R8.2, R10.2, U1.13 (GND)
GPIO: J5.4, U1.7 (PB08_A6_D6_TX)
LIMIT_SW_0: C2.1, R12.1, U1.11 (PA6_A10_D10_MOSI)
MS1: A1.10 (MS1), R2.1, U1.8 (PB09_A7_D7_RX)
MS2: A1.11 (MS2), R3.1, U1.9 (PA7_A8_D8_SCK)
MS3: A1.12 (MS3), R4.1, U1.10 (PA5_A9_D9_MISO)
unnamed: A1.13 (~RESET), A1.14 (~SLEEP)
unnamed: D1.1 (K), R8.1
unnamed: D2.1 (K), U1.14 (5V)
unnamed: D4.1 (K), R10.1
unnamed: J6.1, J7.1, R11.2, R12.2
PWM_S: J3.1, U1.4 (PA11_A3_D3)
SCL: J5.5, U1.6 (PA9_A5_D5_SCL)
SDA: J5.6, U1.5 (PA8_A4_D4_SDA)
STEP: A1.15 (STEP), U1.1 (PA02_A0_D0)
VCC: C3.1, D1.2 (A), D2.2 (A), J3.2, J5.3
VPP: A1.8 (VMOT), C1.1, D4.2 (A), J5.1, J5.2

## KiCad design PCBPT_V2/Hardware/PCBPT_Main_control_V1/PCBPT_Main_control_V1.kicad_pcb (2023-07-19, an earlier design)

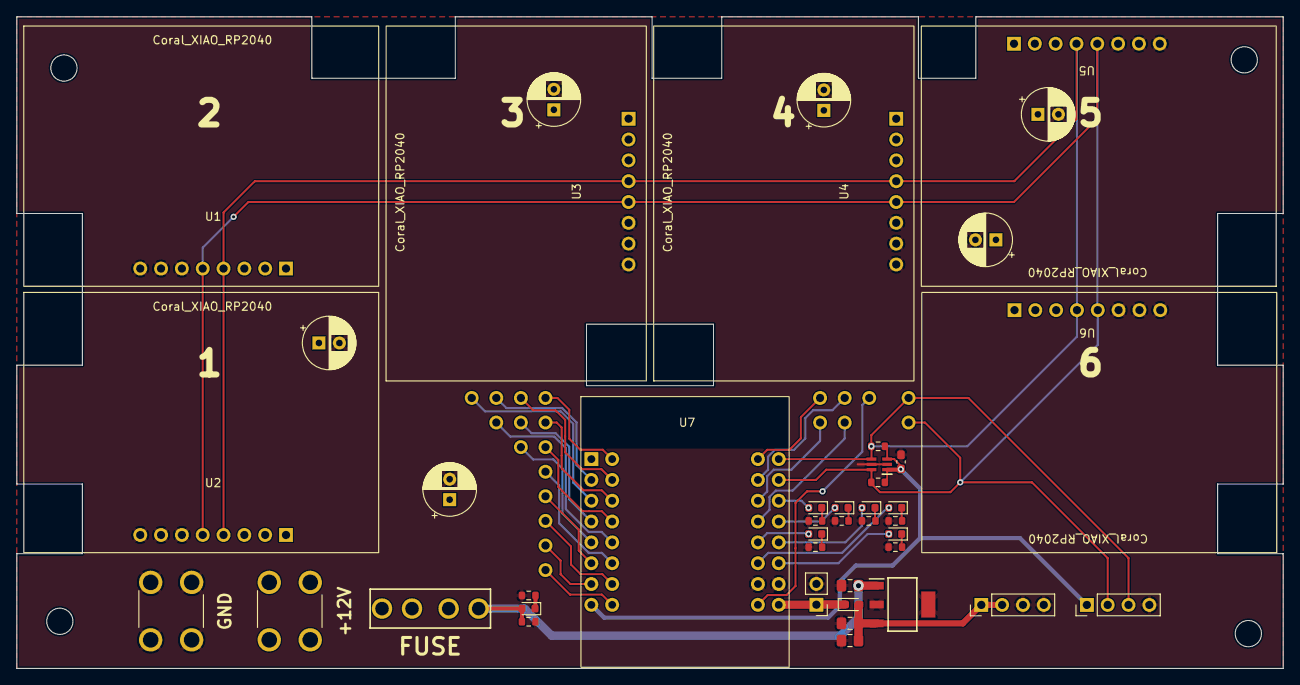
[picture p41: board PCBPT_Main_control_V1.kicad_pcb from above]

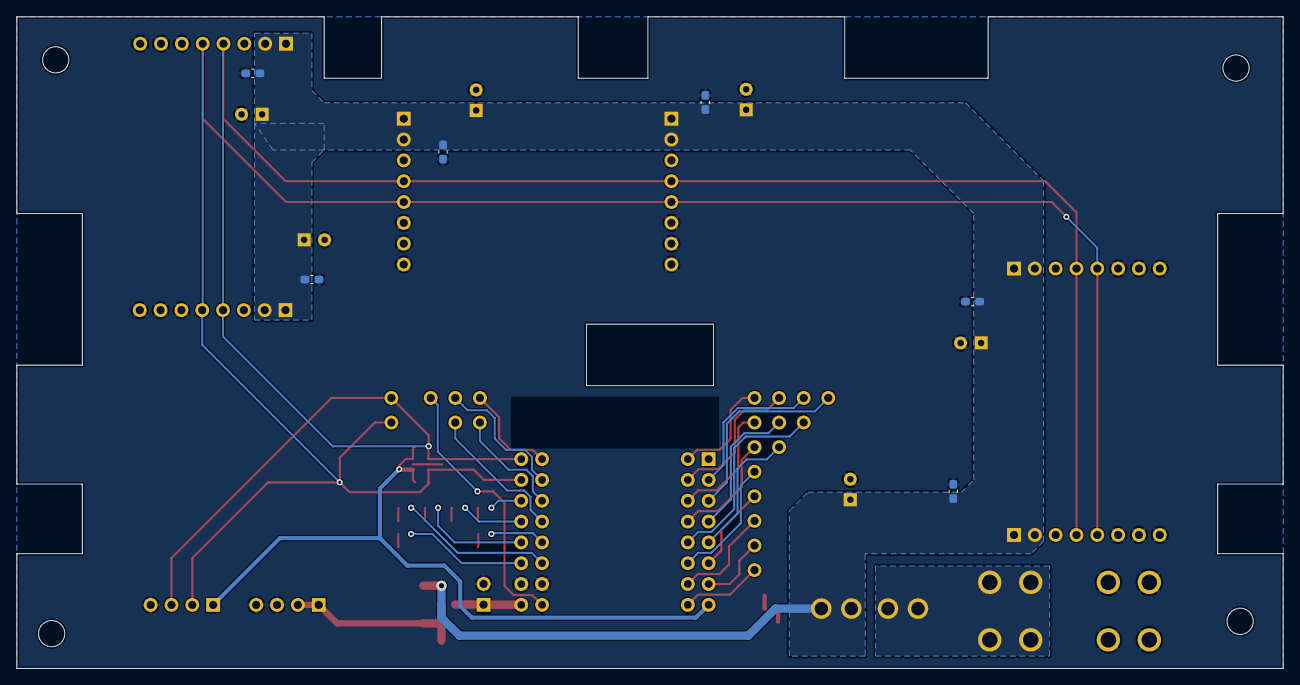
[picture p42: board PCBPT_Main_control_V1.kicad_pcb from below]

Board: 2 copper layers, 154.5 x 79.5 mm, 74 parts (6 on the bottom side), 40 nets.

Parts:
C1, C2, C3, C4, C5, C7: 0.1uF; C_0603_1608Metric_Pad1.08x0.95mm_HandSolder
C6: 0.01uF; C_0603_1608Metric_Pad1.08x0.95mm_HandSolder
C8, C9, C10, C11, C12, C13: 100uF; CP_Radial_D6.3mm_P2.50mm
C15: 0.47uF; C_0805_2012Metric_Pad1.18x1.45mm_HandSolder
C16: 22uF; C_0805_2012Metric_Pad1.18x1.45mm_HandSolder
C17: 0.1uF; C_0805_2012Metric_Pad1.18x1.45mm_HandSolder
D1, D2, D3, D4, D5, D6, D7: LED_Small_Filled; LED_0603_1608Metric
D8: Schottky; D_0603_1608Metric_Pad1.05x0.95mm_HandSolder
H1, H2, H3, H4: MountingHole; MountingHole_3.2mm_M3_DIN965
IC1: LM2940IMP-5.0_NOPB; SOT230P700X180-4N
IC2: LTC4311CSC6#TRPBF; SOT65P210X100-6N
J1: Fan; PinHeader_1x02_P2.54mm_Vertical
J2, J3: 8191-SEMS; 8191SEMS
J4, J8: Conn_01x04_Pin; PinHeader_1x04_P2.54mm_Vertical
R1, R2, R3, R4, R5, R6, R7, R8, R9: 10k; R_0603_1608Metric
R10: 499K; R_0603_1608Metric
TP1, TP2, TP3, TP4, TP5, TP6, TP7, TP8, TP11, TP12, TP13, TP14, TP15, TP16, TP17, TP18, TP19, TP20, TP21, TP22, TP23: TestPoint; 1_pin_sig
U1, U2, U3, U4, U5, U6: XIAO_RP2040_STEPPER_MODULE; Coral_XIAO_RP2040_stepper_ctrl
U7: Wemos/Lolin S2 mini; wemos S2 mini
U8: 3544-2

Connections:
+5V: D8.1 (K), J1.1, U7.9 (VBUS)
+12V: J2.1, J2.2, J2.3, J2.4, U8.1, U8.2
/ESP32S2_module/IND1: D2.2 (A), U7.28 (IO21)
/ESP32S2_module/IND2: D5.2 (A), U7.14 (IO35)
/ESP32S2_module/IND3: D3.2 (A), U7.13 (IO33)
/ESP32S2_module/IND4: D6.2 (A), U7.12 (IO18)
/ESP32S2_module/IND5: D4.2 (A), U7.27 (IO17)
/ESP32S2_module/IND6: D7.2 (A), U7.11 (IO16)
GND: C1.2, C2.2, C3.2, C4.2, C5.2, C6.2, C7.2, C8.2, C9.2, C10.2, C11.2, C12.2, C13.2, C15.2, C16.2, C17.2, IC1.2 (GND_1), IC1.4 (GND_2), IC2.2 (GND_1), IC2.5 (GND_2), J1.2, J3.1, J3.2, J3.3, J3.4, J4.3, J4.4, J8.4, R1.2, R2.2, R3.2, R4.2, R5.2, R6.2, R7.2, R10.1, U1.6 (GND), U1.7 (GND), U1.8 (GND), U2.6 (GND), U2.7 (GND), U2.8 (GND), U3.6 (GND), U3.7 (GND), U3.8 (GND), U4.6 (GND), U4.7 (GND), U4.8 (GND), U5.6 (GND), U5.7 (GND), U5.8 (GND), U6.6 (GND), U6.7 (GND), U6.8 (GND), U7.10 (GND), U7.26 (GND)
unnamed: D1.1 (K), R1.1
unnamed: D2.1 (K), R2.1
unnamed: D3.1 (K), R3.1
unnamed: D4.1 (K), R4.1
unnamed: D5.1 (K), R5.1
unnamed: D6.1 (K), R6.1
unnamed: D7.1 (K), R7.1
unnamed: TP1.1, U7.17 (IO1)
unnamed: TP6.1, U7.18 (IO2)
unnamed: TP11.1, U7.2 (IO3)
unnamed: TP12.1, U7.19 (IO4)
unnamed: TP16.1, U7.3 (IO5)
unnamed: TP3.1, U7.20 (IO6)
unnamed: TP5.1, U7.4 (IO7)
unnamed: TP18.1, U7.21 (IO8)
unnamed: TP17.1, U7.5 (IO9)
unnamed: TP15.1, U7.22 (IO10)
unnamed: TP13.1, U7.6 (IO11)
unnamed: TP4.1, U7.7 (IO12)
unnamed: TP2.1, U7.23 (IO13)
unnamed: TP14.1, U7.24 (IO14)
unnamed: TP19.1, U7.25 (IO15)
unnamed: TP20.1, U7.29 (IO34)
unnamed: TP22.1, U7.30 (IO36)
unnamed: TP23.1, U7.31 (IO38)
unnamed: TP21.1, U7.32 (IO40)
SCL: IC2.4 (BUS2), J8.3, R9.1, TP8.1, U1.4 (SCL), U2.4 (SCL), U3.4 (SCL), U4.4 (SCL), U5.4 (SCL), U6.4 (SCL), U7.16 (IO39)
SDA: IC2.6 (BUS1), J8.2, R8.1, TP7.1, U1.5 (SDA), U2.5 (SDA), U3.5 (SDA), U4.5 (SDA), U5.5 (SDA), U6.5 (SDA), U7.15 (IO37)
VCC: C6.1, IC2.1 (VCC), IC2.3 (ENABLE), J8.1, R8.2, R9.2, U7.8 (3V3)
VDD: C16.1, C17.1, D8.2 (A), IC1.3 (OUT), J4.1, J4.2
VPP: C1.1, C2.1, C3.1, C4.1, C5.1, C7.1, C8.1, C9.1, C10.1, C11.1, C12.1, C13.1, C15.1, D1.2 (A), IC1.1 (IN), R10.2, U1.1 (VPP), U1.2 (VPP), U2.1 (VPP), U2.2 (VPP), U3.1 (VPP), U3.2 (VPP), U4.1 (VPP), U4.2 (VPP), U5.1 (VPP), U5.2 (VPP), U6.1 (VPP), U6.2 (VPP), U8.3, U8.4

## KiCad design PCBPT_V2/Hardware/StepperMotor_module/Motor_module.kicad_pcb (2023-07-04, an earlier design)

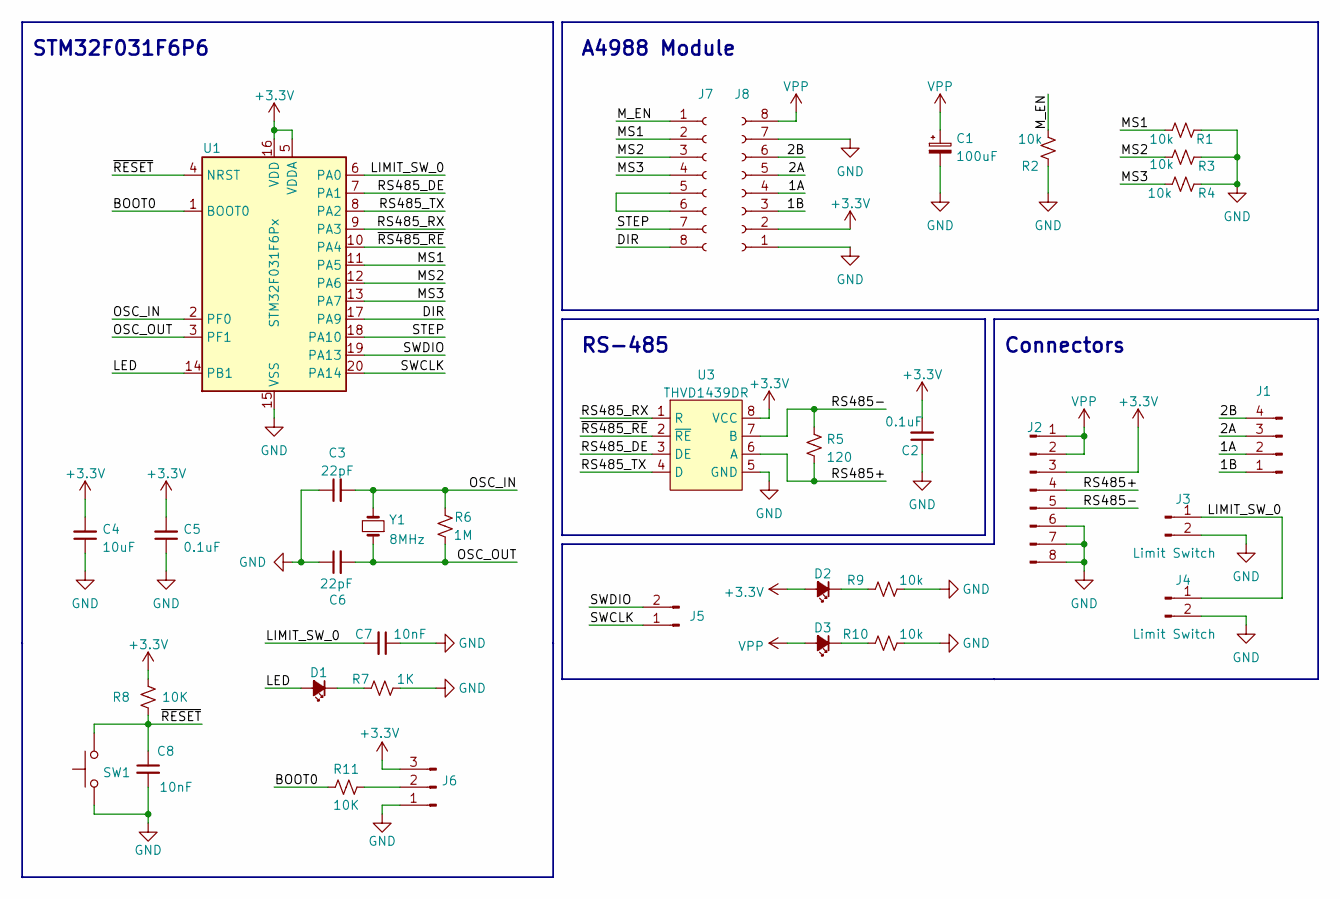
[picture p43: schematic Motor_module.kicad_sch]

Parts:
C1: 100uF; CP_Radial_D5.0mm_P2.50mm
C2, C5: 0.1uF; C_0603_1608Metric
C3, C6: 22pF; C_0603_1608Metric
C4: 10uF; C_0603_1608Metric
C7, C8: 10nF; C_0402_1005Metric
D1, D2, D3: LED_Small_Filled; LED_0603_1608Metric
J1: Limit Switch; PinHeader_1x04_P2.54mm_Vertical
J2: Limit Switch; PinHeader_1x08_P2.54mm_Horizontal
J3, J4: Limit Switch; JST_EH_B2B-EH-A_1x02_P2.50mm_Vertical
J5: Conn_01x08_Male; PinHeader_1x02_P2.54mm_Vertical
J6: Conn_01x04_Male; PinHeader_1x03_P2.54mm_Vertical
J7, J8: Conn_01x08_Female; PinSocket_1x08_P2.54mm_Vertical
R1, R2, R3, R4, R9, R10: 10k; R_0603_1608Metric
R5: 120; R_0603_1608Metric
R6: 1M; R_0603_1608Metric
R7: 1K; R_0603_1608Metric
R8, R11: 10K; R_0603_1608Metric
SW1: SW_Push; SW_Push_1P1T_NO_CK_KMR2
U1: STM32F031F6Px; TSSOP-20_4.4x6.5mm_P0.65mm
U3: THVD1439DR; PowerIntegrations_SO-8
Y1: 8MHz; Crystal_HC18-U_Vertical

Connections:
+3V3: C2.2, C4.2, C5.2, D2.2 (A), J2.3, J6.3, J8.2, R8.2, U1.5 (VDDA), U1.16 (VDD), U3.8 (VCC)
/1A: J1.2, J8.4
/1B: J1.1, J8.3
/2A: J1.3, J8.5
/2B: J1.4, J8.6
/BOOT0: R11.1, U1.1 (BOOT0)
/DIR: J7.8, U1.17 (PA9)
/LED: D1.2 (A), U1.14 (PB1)
/LIMIT_SW_0: C7.2, J3.1, J4.1, U1.6 (PA0)
/MS1: J7.2, R1.1, U1.11 (PA5)
/MS2: J7.3, R3.1, U1.12 (PA6)
/MS3: J7.4, R4.1, U1.13 (PA7)
/M_EN: J7.1, R2.1
/OSC_IN: C3.2, R6.2, U1.2 (PF0), Y1.2
/OSC_OUT: C6.2, R6.1, U1.3 (PF1), Y1.1
/RS485+: J2.4, R5.2, U3.6 (A)
/RS485-: J2.5, R5.1, U3.7 (B)
/RS485_DE: U1.7 (PA1), U3.3 (DE)
/RS485_RX: U1.9 (PA3), U3.1 (R)
/RS485_TX: U1.8 (PA2), U3.4 (D)
/STEP: J7.7, U1.18 (PA10)
/SWCLK: J5.1, U1.20 (PA14)
/SWDIO: J5.2, U1.19 (PA13)
/~RESET: C8.1, R8.1, SW1.2, U1.4 (NRST)
/~RS485_RE: U1.10 (PA4), U3.2 (~RE)
GND: C1.2, C2.1, C3.1, C4.1, C5.1, C6.1, C7.1, C8.2, J2.6, J2.7, J2.8, J3.2, J4.2, J6.1, J8.1, J8.7, R1.2, R2.2, R3.2, R4.2, R7.2, R9.2, R10.2, SW1.1, U1.15 (VSS), U3.5 (GND)
unnamed: D1.1 (K), R7.1
unnamed: D2.1 (K), R9.1
unnamed: D3.1 (K), R10.1
unnamed: J6.2, R11.2
unnamed: J7.5, J7.6
VPP: C1.1, D3.2 (A), J2.1, J2.2, J8.8

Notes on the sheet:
STM32F031F6P6
RS-485
A4988 Module
Connectors

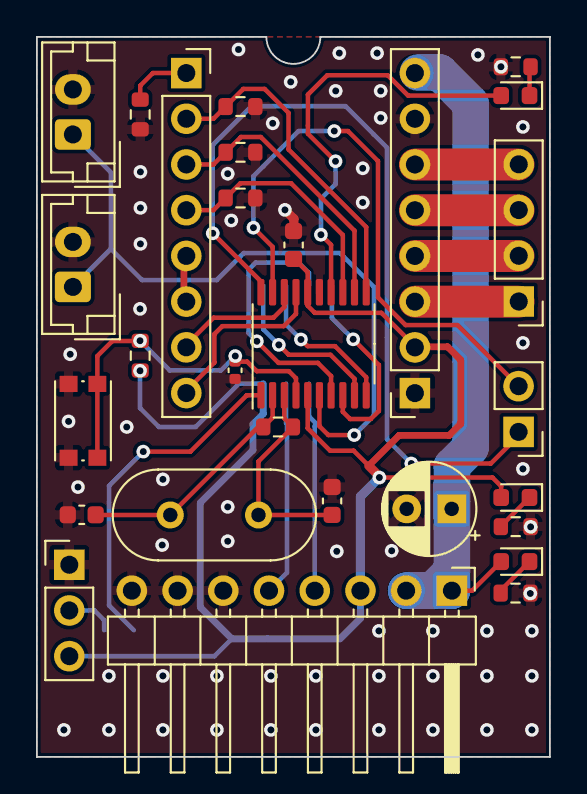
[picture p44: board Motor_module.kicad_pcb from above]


Board: 2 copper layers, 28.5 x 40.0 mm, 34 parts (6 on the bottom side), 32 nets.

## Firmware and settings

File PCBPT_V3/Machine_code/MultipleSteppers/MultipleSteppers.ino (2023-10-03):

// MultiStepper.pde
// -*- mode: C++ -*-
//
// Shows how to multiple simultaneous steppers
// Runs one stepper forwards and backwards, accelerating and decelerating
// at the limits. Runs other steppers at the same time
//
// Copyright (C) 2009 Mike McCauley
// $Id: MultiStepper.pde,v 1.1 2011/01/05 01:51:01 mikem Exp mikem $

#include <AccelStepper.h>

AccelStepper stepper3(AccelStepper::DRIVER, D15, D14);

void setup() {  
  stepper3.setMaxSpeed(2000);
  stepper3.setAcceleration(6000);
  stepper3.moveTo(500); 
}

void loop() {
  // Change direction at the limits
  if (stepper3.distanceToGo() == 0) {
    delay(1000);
	  stepper3.moveTo(-stepper3.currentPosition());
  }

  stepper3.run();
}

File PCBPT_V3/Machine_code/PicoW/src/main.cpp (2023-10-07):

//
// Created by Fangzheng on 9/5/2023.
//

#include <stdio.h>
#include <string>
#include <iostream>

#include "Arduino.h"
#include "pico/stdlib.h"

#include "hardware/address_mapped.h"
#include "hardware/platform_defs.h"
#include "hardware/uart.h"

#include "hardware/structs/uart.h"
#include "hardware/resets.h"
#include "hardware/clocks.h"
#include "hardware/timer.h"

#include "pico/assert.h"
#include "pico.h"
#include "hardware/gpio.h"
#include "hardware/adc.h"
#include "pico/binary_info.h"
#include "hardware/i2c.h"

#include "stepper_FZ.h"
#include "system.h"
#include "comm.h"

const uint LED_PIN = PICO_DEFAULT_LED_PIN;

void setup() {
  pin_init();
  comm_init();
  home_machine();
}

void loop() {
  comm_update();
};

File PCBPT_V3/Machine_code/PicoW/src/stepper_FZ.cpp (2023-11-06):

#include <AccelStepper.h>

#include "stepper_FZ.h"
#include "comm.h"
#include "system.h"

float motion_A = 0.0;
float motion_B = 0.0;
float motion_X = 0.0;
float motion_Y = 0.0;

AccelStepper stepper1(AccelStepper::DRIVER, D15, D14); // 
AccelStepper stepper2(AccelStepper::DRIVER, D11, D10); //
AccelStepper stepper3(AccelStepper::DRIVER, D7, D6);   //
AccelStepper stepper4(AccelStepper::DRIVER, D13, D12); // 
AccelStepper stepper5(AccelStepper::DRIVER, D9, D8);   //
AccelStepper stepper6(AccelStepper::DRIVER, D5, D4);   //
AccelStepper stepper7(AccelStepper::DRIVER, D3, D2);   // 
AccelStepper stepper8(AccelStepper::DRIVER, D1, D0);   // 

void stepper_init(uint8_t speed_option) {
  if (speed_option == MOTION_SPEED) {
    stepper1.setMaxSpeed(1000);
    stepper1.setAcceleration(2000);
    stepper1.setCurrentPosition(MOTOR_1_HOME_POS);

    stepper2.setMaxSpeed(1000);
    stepper2.setAcceleration(2000);
    stepper2.setCurrentPosition(MOTOR_2_HOME_POS);

    stepper3.setMaxSpeed(3000);
    stepper3.setAcceleration(6000);
    stepper3.setCurrentPosition(MOTOR_3_HOME_POS);

    stepper4.setMaxSpeed(1000);
    stepper4.setAcceleration(2000);
    stepper4.setCurrentPosition(MOTOR_4_HOME_POS);

    stepper5.setMaxSpeed(1000);
    stepper5.setAcceleration(2000);
    stepper5.setCurrentPosition(MOTOR_5_HOME_POS);

    stepper6.setMaxSpeed(3000);
    stepper6.setAcceleration(6000);
    stepper6.setCurrentPosition(MOTOR_6_HOME_POS);

    // stepper7.setMaxSpeed(2000);
    // stepper7.setAcceleration(6000);
    // stepper1.setCurrentPosition(MOTOR_7_HOME_POS);

    // stepper8.setMaxSpeed(2000);
    // stepper8.setAcceleration(6000);
    // stepper1.setCurrentPosition(MOTOR_8_HOME_POS);
  }
  else {
    stepper1.setMaxSpeed(500);
    stepper1.setAcceleration(1000);
    stepper2.setMaxSpeed(500);
    stepper2.setAcceleration(1000);
    stepper3.setMaxSpeed(500);
    stepper3.setAcceleration(1000);
    stepper4.setMaxSpeed(500);
    stepper4.setAcceleration(1000);
    stepper5.setMaxSpeed(500);
    stepper5.setAcceleration(1000);
    stepper6.setMaxSpeed(500);
    stepper6.setAcceleration(1000);
    // stepper7.setMaxSpeed(500);
    // stepper7.setAcceleration(1000);
    // stepper8.setMaxSpeed(500);
    // stepper8.setAcceleration(1000);
  }
}

void home_stepper(AccelStepper *stepper, int pos, uint8_t limit_sw_pin, long home_pos) {
  stepper->move(pos);
  while (digitalRead(limit_sw_pin)) {
    stepper->run();
  }
  stepper->setCurrentPosition(home_pos);
}

void home_machine(void) {
  stepper_init(HOME_SPEED);

  home_stepper(&stepper3, -50000, LIMIT_SW_3_PIN, MOTOR_3_HOME_POS);
  home_stepper(&stepper1, -50000, LIMIT_SW_1_PIN, MOTOR_1_HOME_POS);
  home_stepper(&stepper2, -50000, LIMIT_SW_2_PIN, MOTOR_2_HOME_POS);

  home_stepper(&stepper6, -50000, LIMIT_SW_6_PIN, MOTOR_6_HOME_POS);
  home_stepper(&stepper4, -50000, LIMIT_SW_4_PIN, MOTOR_4_HOME_POS);
  home_stepper(&stepper5, -50000, LIMIT_SW_5_PIN, MOTOR_5_HOME_POS);

  stepper_init(MOTION_SPEED);
}

void start_motion_L(void) {
  stepper3.moveTo(MOTOR_3_PROBE_INI_POS);

  while(stepper3.distanceToGo()) {
    stepper3.run();
  }

  if (recv_CMD.cmd_type == MANUCAL_CTRL_CMD) {
    if (recv_CMD.check_REG(recv_CMD.CMD_REG, CMD_A_POS)) {
      long pos_A = (recv_CMD.A_position_f)/stepper_res_1;
      stepper1.move(pos_A);
    }
    if (recv_CMD.check_REG(recv_CMD.CMD_REG, CMD_B_POS)) {
      long pos_B = (recv_CMD.B_position_f)/stepper_res_1;
      stepper2.move(pos_B);
    }

    while(stepper1.distanceToGo() || stepper2.distanceToGo()) {
      stepper1.run();
      stepper2.run();
    }
  }

  else {
    if (recv_CMD.check_REG(recv_CMD.CMD_REG, CMD_A_POS)) {
      long pos_A = (recv_CMD.A_position_f + LASER_BIAS_1)/stepper_res_1;
      stepper1.moveTo(pos_A);
    }
    if (recv_CMD.check_REG(recv_CMD.CMD_REG, CMD_B_POS)) {
      long pos_B = (recv_CMD.B_position_f + LASER_BIAS_2)/stepper_res_1;
      stepper2.moveTo(pos_B);
    }

    while(stepper1.distanceToGo() || stepper2.distanceToGo()) {
      stepper1.run();
      stepper2.run();
    }
  }

  if (recv_CMD.cmd_type == PROBE_CMD) {
    stepper3.moveTo(MOTOR_3_PROBE_POS);

    while(stepper3.distanceToGo()) {
      stepper3.run();
    }
  }
}

void start_motion_R(void) {
  stepper6.moveTo(MOTOR_6_PROBE_INI_POS);

  while(stepper6.distanceToGo()) {
    stepper6.run();
  }

  if (recv_CMD.cmd_type == MANUCAL_CTRL_CMD) {
    if (recv_CMD.check_REG(recv_CMD.CMD_REG, CMD_X_POS)) {
      long pos_X = (recv_CMD.X_position_f)/stepper_res_1;
      stepper4.move(pos_X);
    }
    if (recv_CMD.check_REG(recv_CMD.CMD_REG, CMD_Y_POS)) {
      long pos_Y = (recv_CMD.Y_position_f)/stepper_res_1;
      stepper5.move(pos_Y);
    }

    while(stepper4.distanceToGo() || stepper5.distanceToGo()) {
      stepper4.run();
      stepper5.run();
    }
  }

  else {
    if (recv_CMD.check_REG(recv_CMD.CMD_REG, CMD_X_POS)) {
      long pos_X = (LASER_BIAS_3 - recv_CMD.X_position_f)/stepper_res_1;
      stepper4.moveTo(pos_X);
    }
    if (recv_CMD.check_REG(recv_CMD.CMD_REG, CMD_Y_POS)) {
      long pos_Y = (recv_CMD.Y_position_f + LASER_BIAS_4)/stepper_res_1;
      stepper5.moveTo(pos_Y);
    }

    while(stepper4.distanceToGo() || stepper5.distanceToGo()) {
      stepper4.run();
      stepper5.run();
    }
  }

  if (recv_CMD.cmd_type == PROBE_CMD) {
    stepper6.moveTo(MOTOR_6_PROBE_POS);

    while(stepper6.distanceToGo()) {
      stepper6.run();
    }
  }
}

void start_motion_X(uint8_t left, float left_pos, uint8_t right, float right_pos, uint8_t move_or_move_To) {
  if (move_or_move_To == MOVE) {
    if (left) {
      long pos_A = left_pos/stepper_res_1;
      stepper1.move(pos_A);
    }

    if (right) {
      long pos_X = right_pos/stepper_res_1;
      stepper4.move(pos_X);
    }

    while(stepper1.distanceToGo() || stepper4.distanceToGo()) {
      stepper1.run();
      stepper4.run();
    }
  }

  if (move_or_move_To == MOVETO) {
    if (left) {
      long pos_A = (left_pos + LASER_BIAS_1)/stepper_res_1;
      stepper1.moveTo(pos_A);
    }

    if (right) {
      long pos_X = (LASER_BIAS_3 - right_pos)/stepper_res_1;
      stepper4.moveTo(pos_X);
    }

    while(stepper1.distanceToGo() || stepper4.distanceToGo()) {
      stepper1.run();
      stepper4.run();
    }
  }
}
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

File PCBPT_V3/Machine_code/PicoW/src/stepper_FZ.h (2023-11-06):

//
// Created by l1534 on 9/13/2023.
//

#ifndef __STEPPER_FZ_H
#define __STEPPER_FZ_H

#include "Arduino.h"

#define HOME_SPEED   0
#define MOTION_SPEED 1

#define stepper_res_1 0.1 // how much the linear motion is in one step

#define MOTOR_1_HOME_POS 0
#define MOTOR_2_HOME_POS 0
#define MOTOR_3_HOME_POS 0
#define MOTOR_4_HOME_POS 0
#define MOTOR_5_HOME_POS 0
#define MOTOR_6_HOME_POS 0

#define MOTOR_3_PROBE_POS     2700
#define MOTOR_3_PROBE_INI_POS 1500

#define MOTOR_6_PROBE_POS     2750
#define MOTOR_6_PROBE_INI_POS 1500

#define LASER_BIAS_1 19
#define LASER_BIAS_2 9

#define LASER_BIAS_3 125
#define LASER_BIAS_4 13.7
// #define LASER_BIAS_3 127.5
// #define LASER_BIAS_4 11.7

#define UNPROBE 0
#define PROBE   1

extern float motion_A;
extern float motion_B;
extern float motion_X;
extern float motion_Y;

#define X_SAFETY        3
#define X_SAFETY_SINGLE 100

#define MOVE   0
#define MOVETO 1

extern void stepper_init(uint8_t speed_option);

extern void start_motion_L(void);
extern void start_motion_R(void);

extern void home_machine(void);
extern void home_stepper(void);

extern void start_motion_X(uint8_t left, float left_pos, uint8_t right, float right_pos, uint8_t move_or_move_To);
extern void start_motion_Y(uint8_t left, float left_pos, uint8_t right, float right_pos, uint8_t move_or_move_To);
extern void probe(uint8_t probe_action, uint8_t left, uint8_t right);

#endif //PICOW_STEPPER_FZ_H

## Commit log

2021-10-17 udated by FZ
    [3mm_shaft.sldprt, 90592A085_Steel Hex Nut.SLDPRT, 90710A030_18-8 Stainless Steel Thin Hex Nut.SLDPRT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]
2023-07-19 Add pcbpt upload interface
2023-07-28 Adding PCB view
    [platform_body.stl, platform_clip.stl, platform_lock.stl]
2023-07-28 Adding board edges
